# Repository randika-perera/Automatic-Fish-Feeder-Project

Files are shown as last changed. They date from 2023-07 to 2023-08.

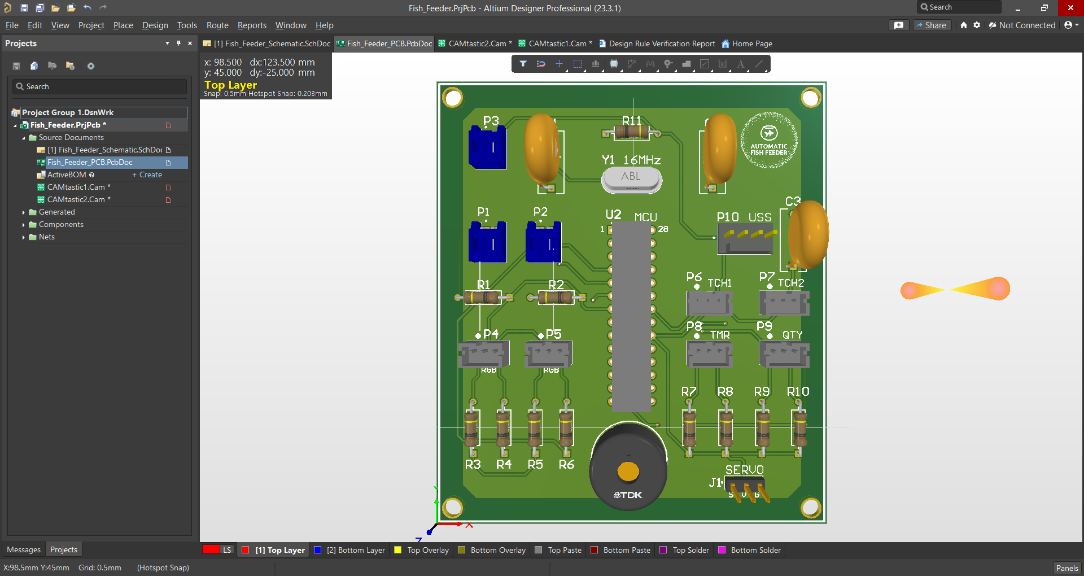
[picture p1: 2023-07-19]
PCB Design/Fish_Feeder/Images/3D View Top.png

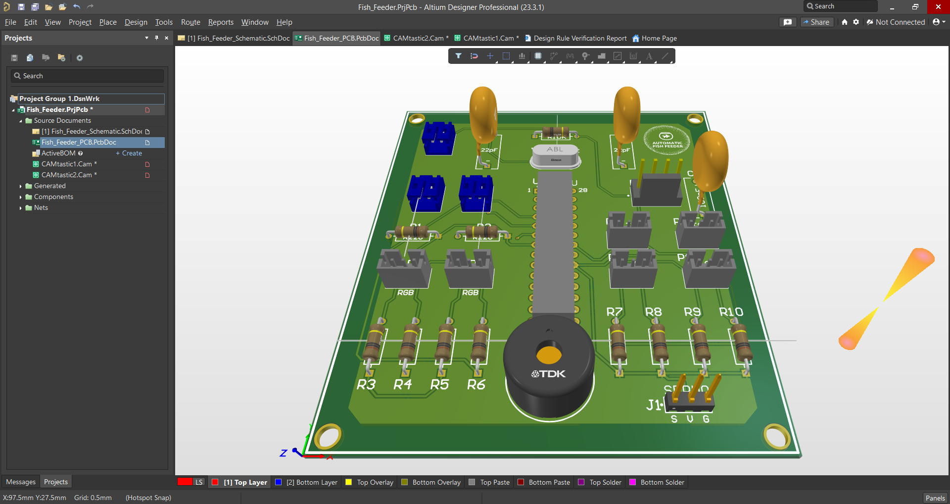
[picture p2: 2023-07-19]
PCB Design/Fish_Feeder/Images/3D View Side.png

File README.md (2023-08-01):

## Automatic Fish Feeder

The goal of this project was to make improvements to an existing market product and make it more marketable. </br>
This was an *individual project* carried out for the *Semester 4 Module EN2160 - Electronic Design Realization.*

The product that was implemented was an automatic fish feeder. </br>
The **improvements** and **extra features** that were incorporated to set it apart from existing products are as follows,
- ***Simple User Interface and Controls*** – Upon market research it was apparent that most of the existing products had heavily cluttered interfaces and control panels. Simplification of the user interface and hence improving the user experience was the biggest focus of this product.
- ***Mountable on both sides*** – This was designed to be mounted on either sides of a fish tank by incorporating replicated indicators and controls on 2 sides.
- ***Level Detection*** – Capable of indicating to the user when the fish food in the storage compartment has gone below a certain level. Indications were done redundantly using both sound and light indications for better notifying the user.
- ***Touch Sensor*** – Instead of using push buttons like existing market products, touch sensors were utilized.

The project involved designing the circuit from scratch according to the set requirements, fabrication of a printed circuit board, hand soldering components, circuit testing and design of a 3D printed enclosure to encase everything in a suitable form factor.

Software tools including *VSCode*, *Arduino IDE*, *Proteus Design Suite*, *Altium Designer* and *SolidWorks* were utilized.

The functional block diagram of the product is given below,

block_diagram

A photo of the final product is given below,



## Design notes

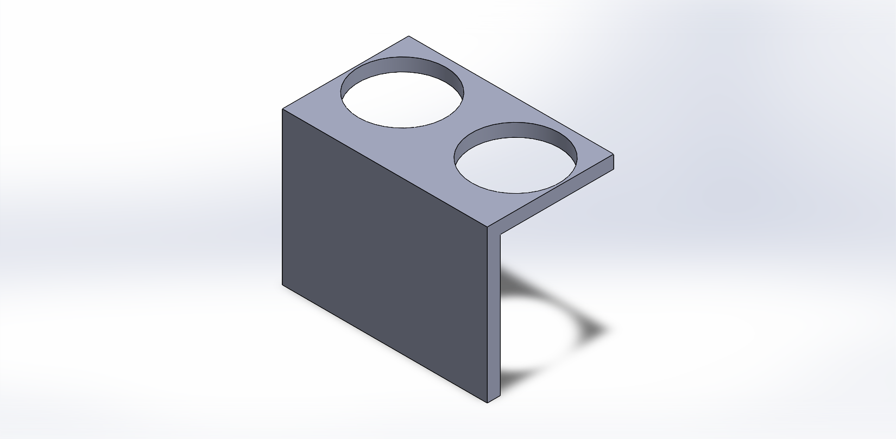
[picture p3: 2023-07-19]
Enclosure Design/Images/Ultrasonic Bracket.PNG

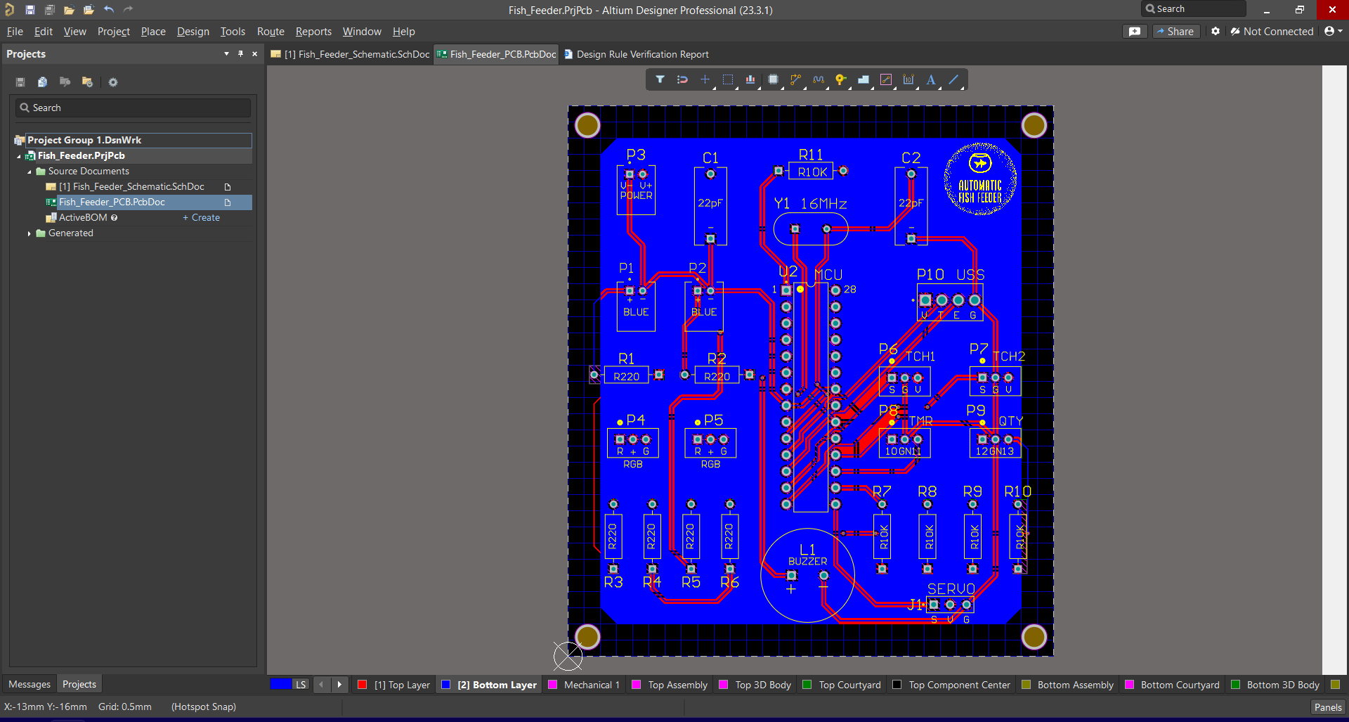
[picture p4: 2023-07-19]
PCB Design/Fish_Feeder/Images/Bottom Layer.png

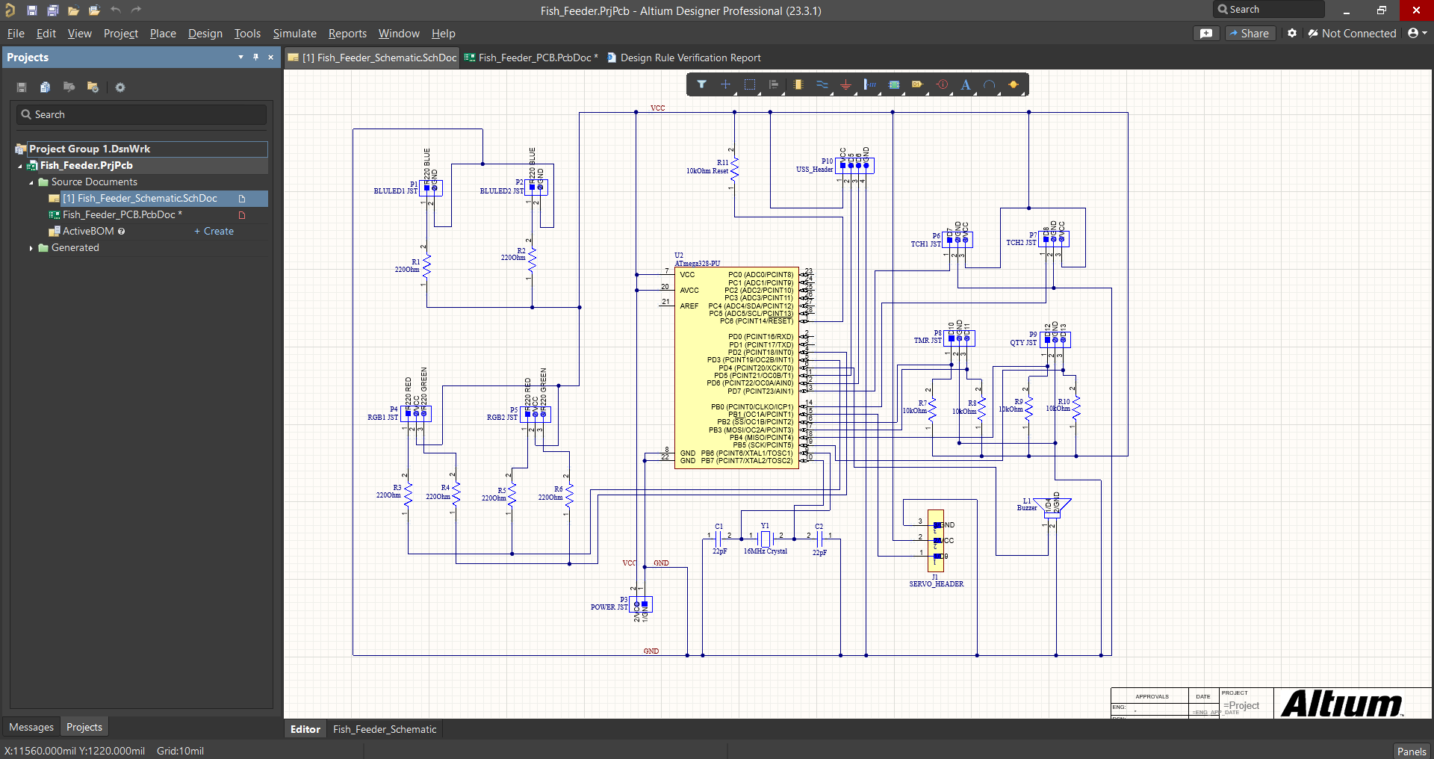
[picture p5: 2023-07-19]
PCB Design/Fish_Feeder/Images/Schematic.png

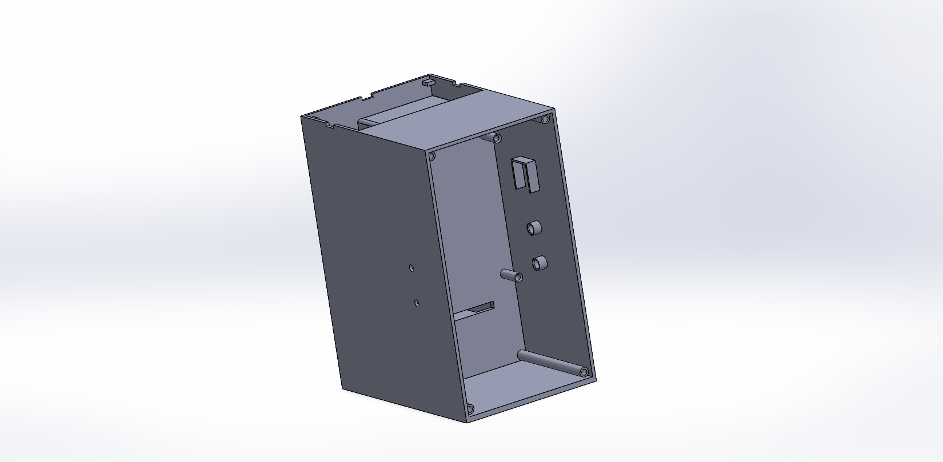
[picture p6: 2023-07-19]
Enclosure Design/Images/Main Body.PNG

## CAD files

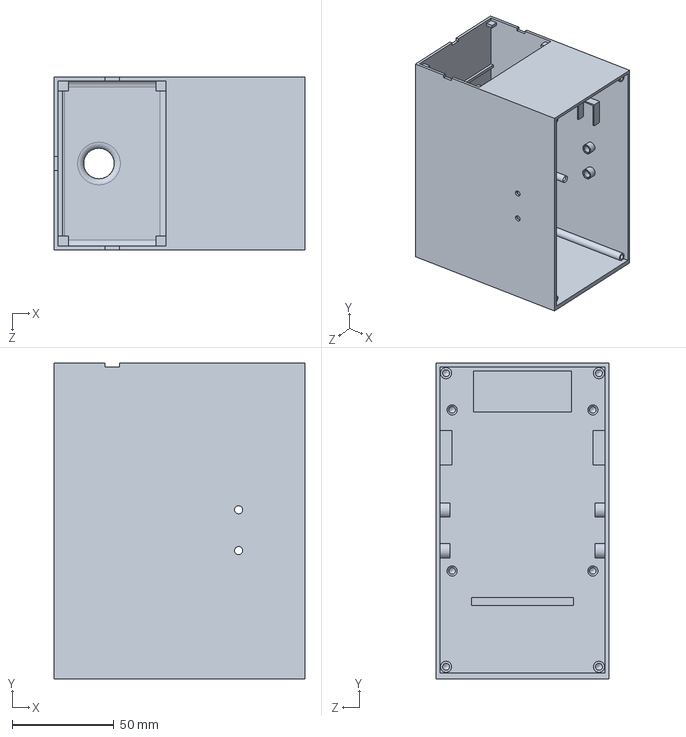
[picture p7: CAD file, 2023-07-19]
Enclosure Design/Main Body.SLDPRT
123.0 x 155.0 x 85.0 mm

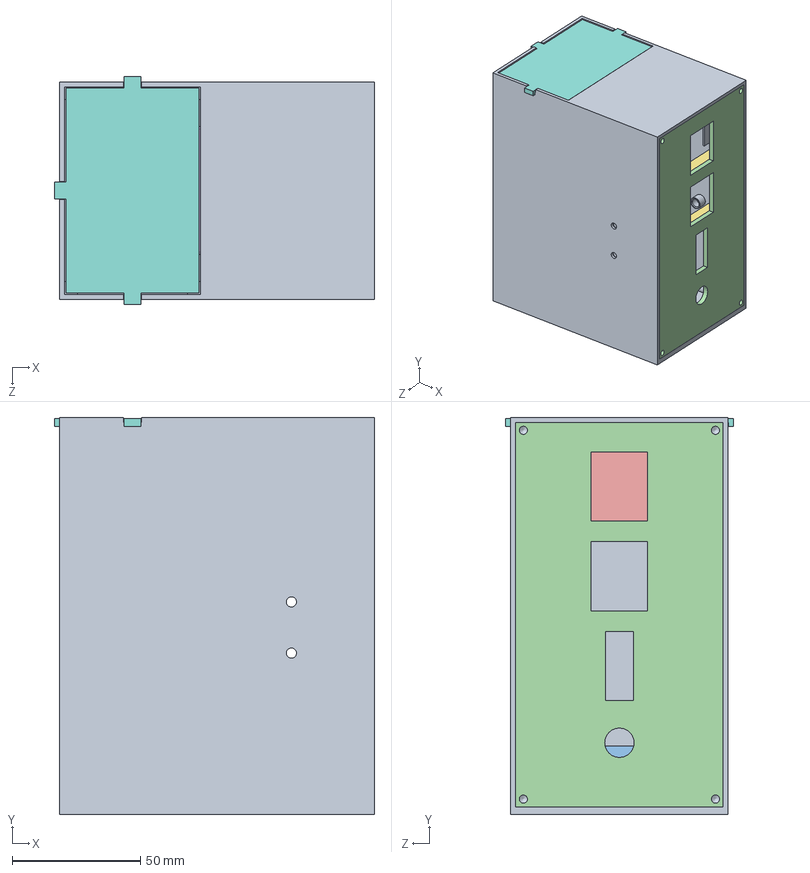
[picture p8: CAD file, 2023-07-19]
Enclosure Design/Assembly/Assembly of Full Enclosure.SLDASM
125.0 x 155.0 x 89.0 mm
Main Body
Servo Arm
Servo Bracket
Side Panel
Ultrasonic Bracket
Ultrasonic Hood
L Beam x 2
Top Lid Modified

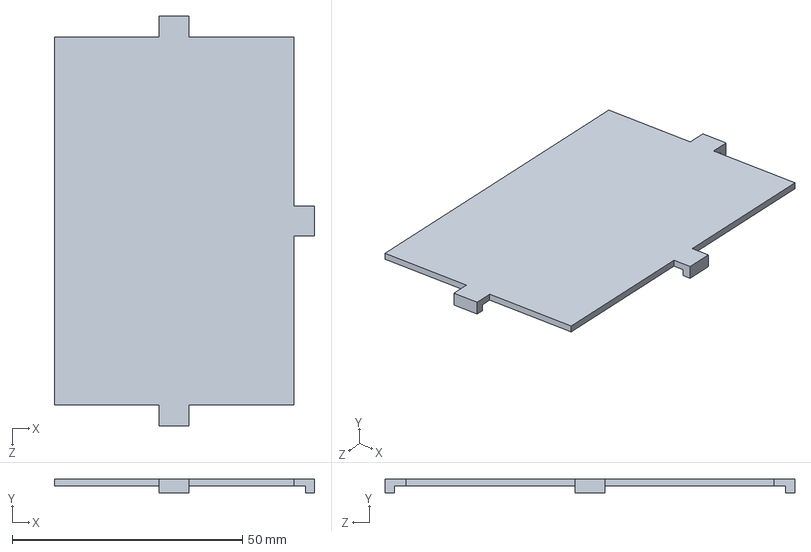
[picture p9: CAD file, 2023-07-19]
Enclosure Design/Assembly/Top Lid Modified.SLDPRT
56.5 x 3.00 x 89.0 mm

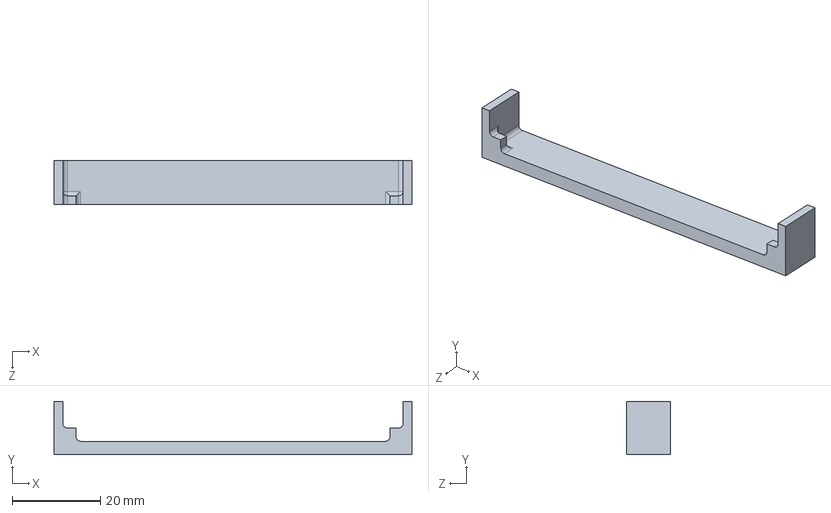
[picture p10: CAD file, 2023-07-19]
Enclosure Design/C Beam.SLDPRT
81.0 x 12.0 x 10.0 mm

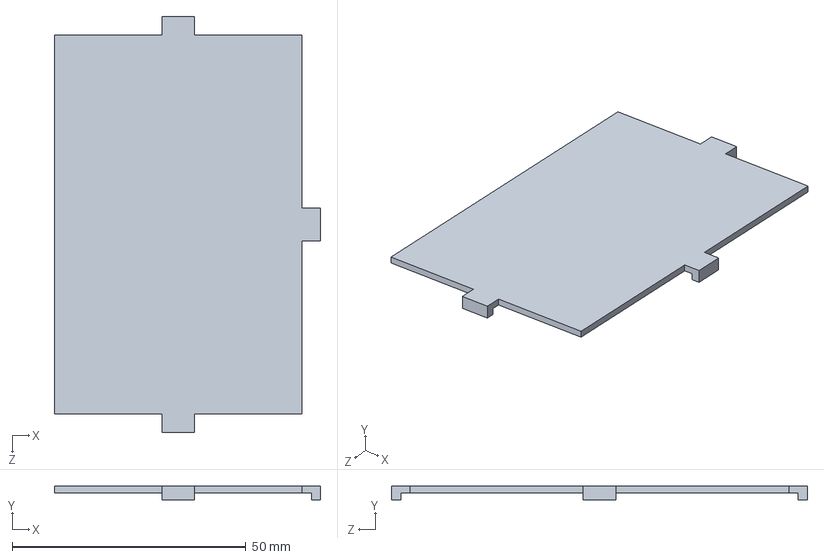
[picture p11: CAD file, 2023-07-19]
Enclosure Design/Assembly/Top Lid.SLDPRT
57.0 x 3.00 x 89.0 mm

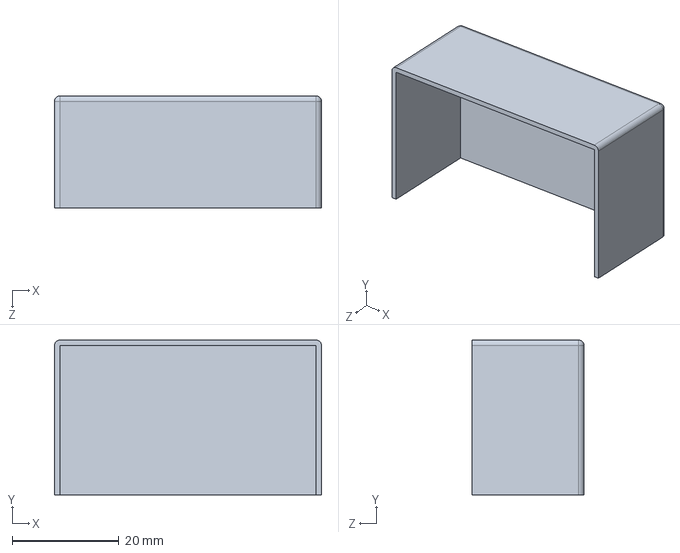
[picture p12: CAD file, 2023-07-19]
Enclosure Design/Ultrasonic Hood.SLDPRT
50.0 x 29.0 x 21.0 mm

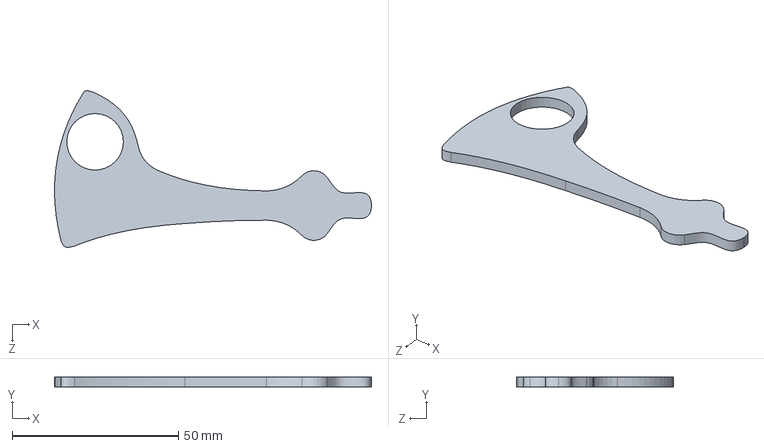
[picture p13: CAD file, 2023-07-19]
Enclosure Design/Assembly/Servo Arm.SLDPRT
95.4 x 3.00 x 47.1 mm

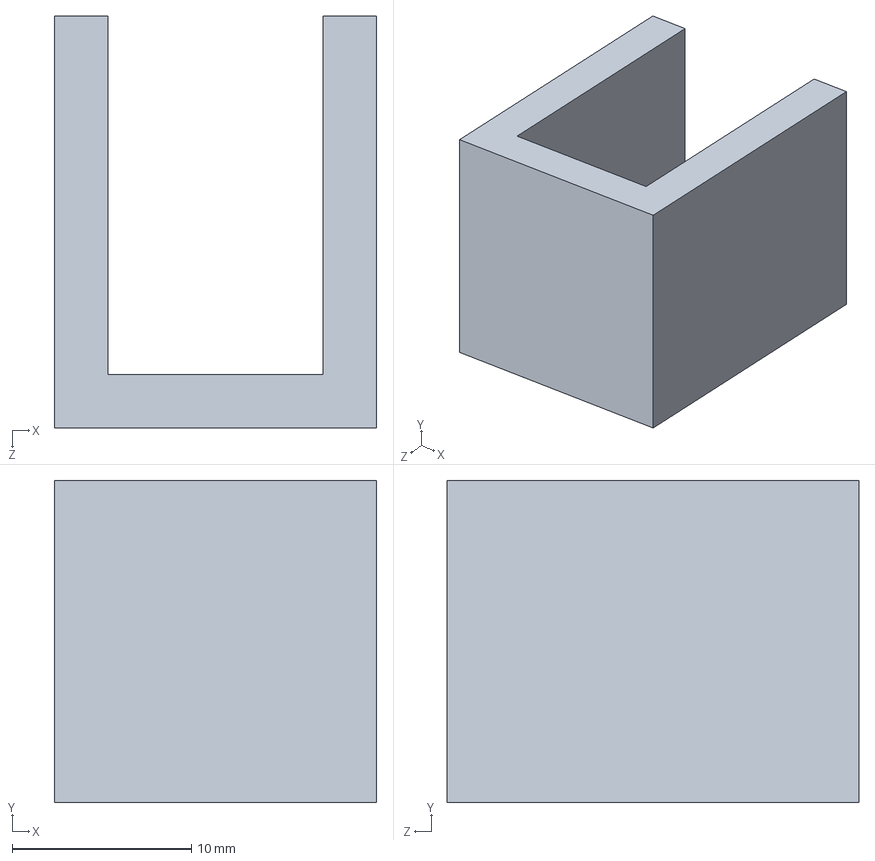
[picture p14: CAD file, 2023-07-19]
Enclosure Design/Servo Bracket.SLDPRT
18.0 x 18.0 x 23.0 mm

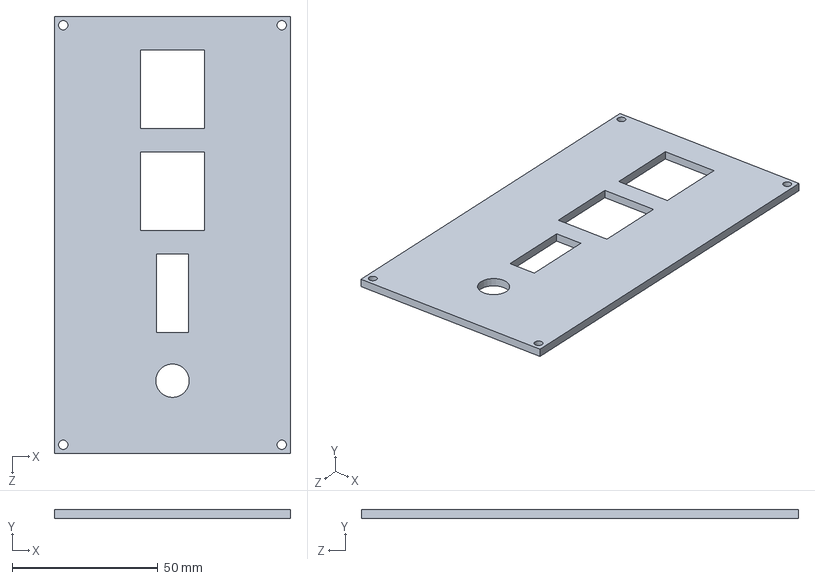
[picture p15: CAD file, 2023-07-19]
Enclosure Design/Assembly/Side Panel.SLDPRT
81.0 x 3.00 x 150.0 mm

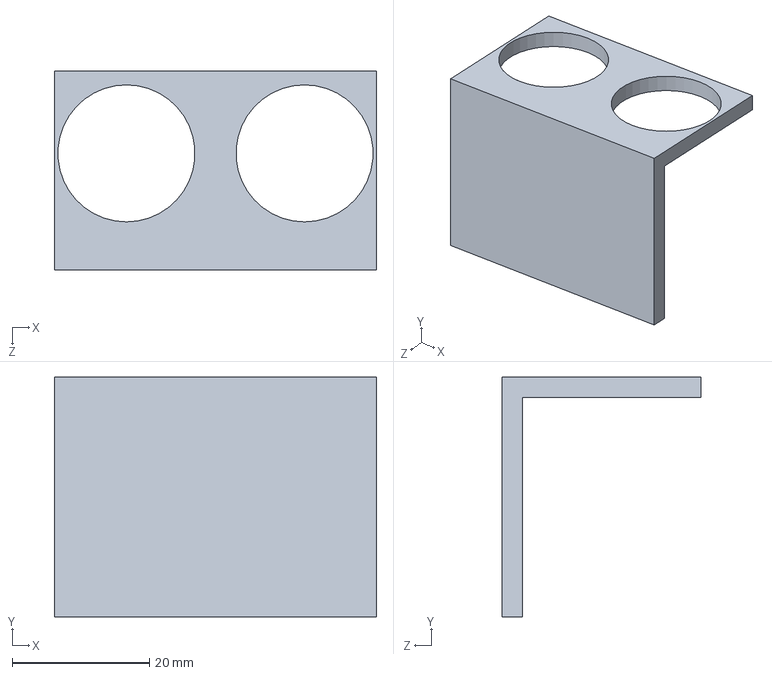
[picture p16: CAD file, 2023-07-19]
Enclosure Design/Assembly/Ultrasonic Bracket.SLDPRT
47.0 x 35.0 x 29.0 mm

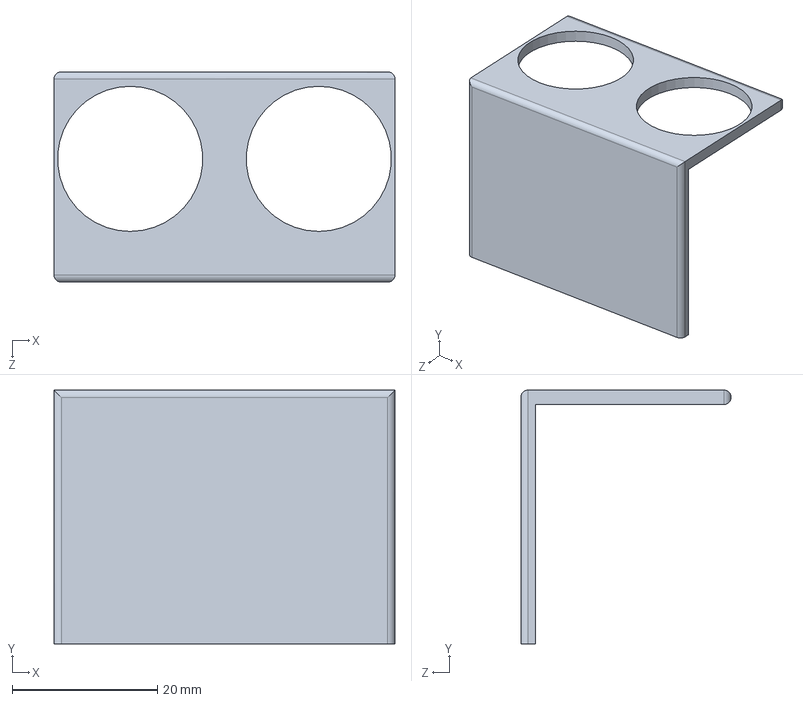
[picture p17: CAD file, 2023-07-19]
Enclosure Design/Ultrasonic Bracket.SLDPRT
47.0 x 35.0 x 29.0 mm

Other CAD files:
Enclosure Design/Assembly/Ultrasonic Hood.SLDPRT
Enclosure Design/C Beam.STL
Enclosure Design/Main Body.STL
Enclosure Design/Servo Arm.STL
Enclosure Design/Servo Bracket.STL
Enclosure Design/Side Panel.STL
Enclosure Design/Top Lid Modified.STL
Enclosure Design/Top Lid.STL
Enclosure Design/Ultrasonic Bracket.STL
Enclosure Design/Ultrasonic Hood.STL

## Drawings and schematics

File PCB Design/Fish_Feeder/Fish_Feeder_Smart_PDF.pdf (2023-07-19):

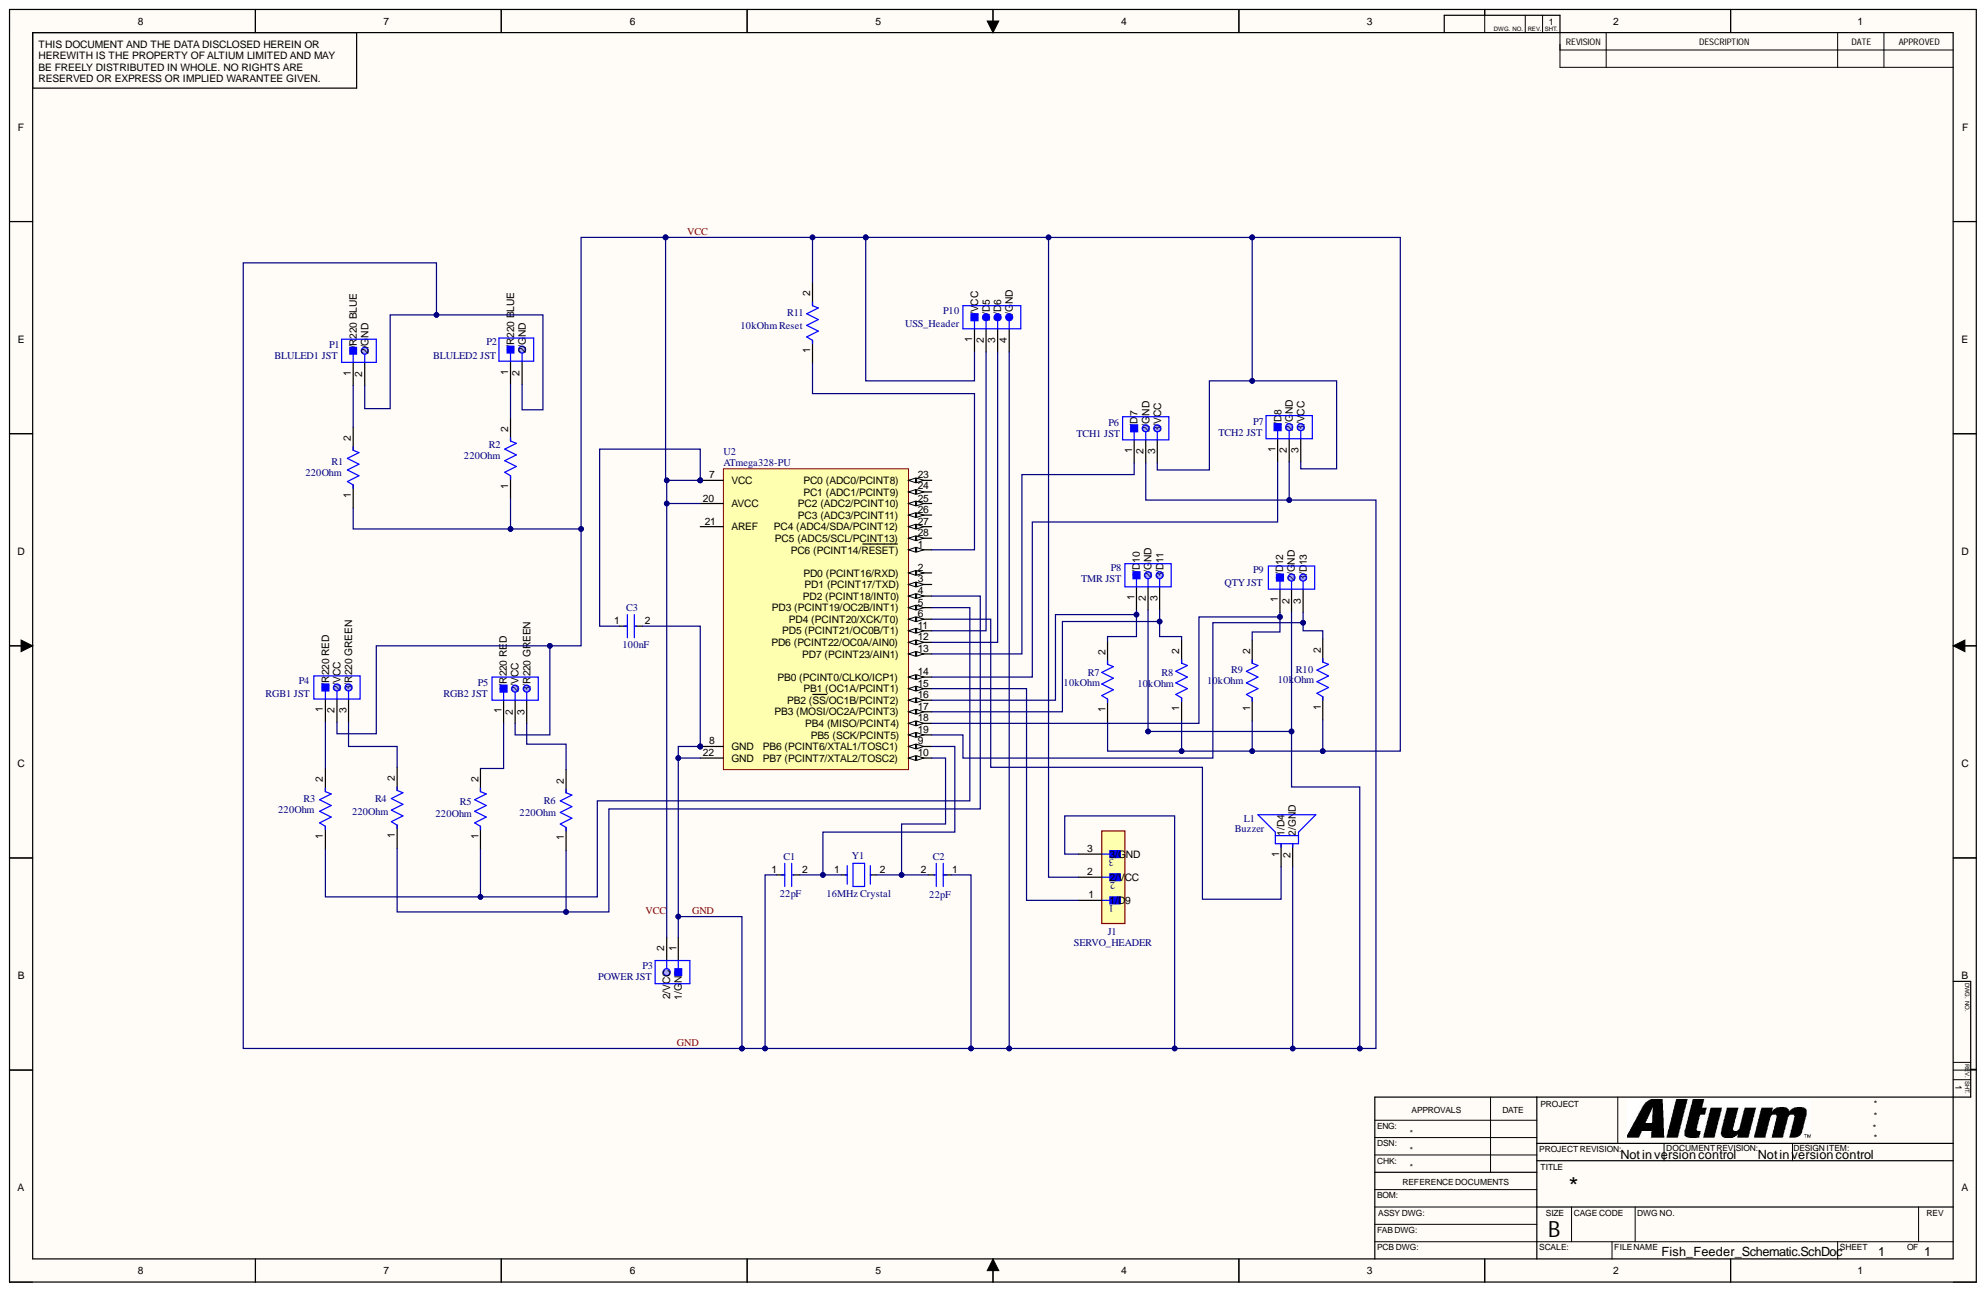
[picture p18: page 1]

T H I S D O C UME N T A N D T H E D AT A D I S C L O S E D H E R E I N O R H E R EWI T H I S T H E P R O P E R T Y O F A LT I UM L IMI T E D A N D MAY B E F R E E LY D I S T R I B U T E D I N WH O L E . N O R I G H T S A R E R E S E R V E D O R E X P R E S S O R IMP L I E D WA R A N T E E G I V E N . | C | REVI S I ON | DE SCRI PT I ON | DAT E | APPROVE D

1 4 | | R 7
1 5 | 1 0 | k O hm | 0 k O | 0 k O hm
1 6
1 7
1 8
1 9

REV. SHT. DWG. NO.

A P PROV A L S | DAT E | PROJE CT | ****

ENG :
** DSN:
CHK : | | TIT L E *

PROJECT RE VISION : Not i n v | ers DOCUM i o n c ENT RE o ntr o VISION l : Not i n | v DE ers SIGN IT i o n E c M o : ntr o l

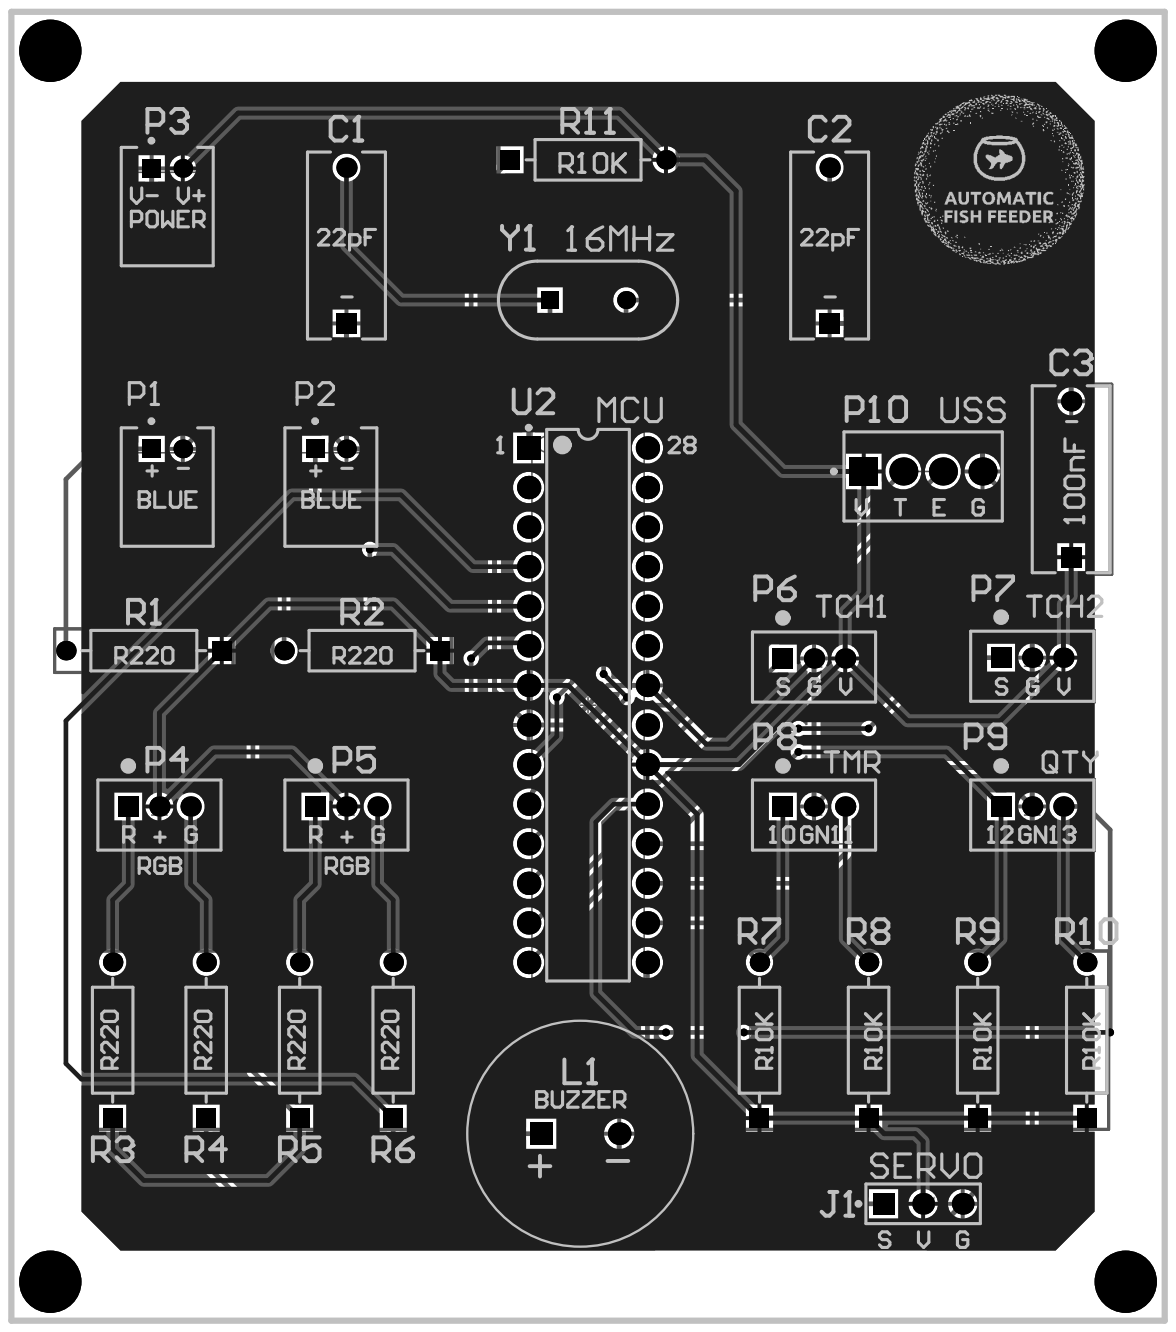
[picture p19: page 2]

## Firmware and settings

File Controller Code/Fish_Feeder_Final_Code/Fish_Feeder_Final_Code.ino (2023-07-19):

/*                                                      Automatic fish food dispenser                                                       */
/*                                        Copyright (C) 2023 Randika Perera.  All rights reserved.                                          */




/*-------------------------------------------  Importing Libraries and Declaration of I/O Pins  --------------------------------------------*/

#include <Servo.h>
Servo myservo;

const int RGB_green_pin=2;
const int RGB_red_pin=3;
const int buzzer_pin=4;
const int uss_trig_pin=5;
const int uss_echo_pin=6;
const int touch_sensor1_pin=7;
const int touch_sensor2_pin=8; 
const int servo_pin=9;
const int tmr_switch_INA_pin=10;
const int tmr_switch_INC_pin=11;
const int qty_switch_INA_pin=12;
const int qty_switch_INC_pin=13;


/*-----------------------------------------------  Declaration of variables and constants  -------------------------------------------------*/

const int fish_food_threshold_level=7;  //If distance between the sensor and surface of fish food is more than 7cm, fish food level is LOW. Else, HIGH.
int current_fish_food_level;

int distance;
int roundeddistance;
long t;

int tmr_switch_INA=1; //  1 or 0
int tmr_switch_INC=1; //  1 or 0
int qty_switch_INA=1; //  1 or 0
int qty_switch_INC=1; //  1 or 0

int tmr_state=1;  //  1:24hour, 2:12hour,   3:8hour
int qty_state=1;  //  1:Low,    2:Medium,   3:High

bool FF_level_state=HIGH; // LOW:Low fish food,  HIGH: Sufficient fish food
bool FF_alarm_state=LOW;  // Alarm can only ring in HIGH state.

const int servo_slot_closed_pos=87;   //Servo position for closed slot (default position).
const int servo_slot_open_pos=66;     //Servo position for opened slot.
int slot_open_delay;                  //Time for which slot remains opened. Depends on qty_state.

//CHANGE THESE DURATIONS AS REQUIRED FOR FINAL PRODUCT
const int low_duration=150;      //Duration to keep slot open for low quantity     : 0.15s  
const int medium_duration=350;   //Duration to keep slot open for medium quantity  : 0.35s  
const int high_duration=500;     //Duration to keep slot open for high quantity    : 0.50s  

unsigned long current_time=0;
unsigned long previous_fishfooddispense_time=0;
unsigned long previous_levelmeasurement_time=0;
unsigned long previous_fflalarm_time=0;

//CHANGE THESE INTERVALS AS REQUIRED FOR FINAL PRODUCT
unsigned long fishfooddispense_interval;                //Depends on tmr_state. If tmrstate=1:24hours, tmrstate=2:12hours, tmrstate=3:8hours.
const unsigned long hour_24_interval = 20000;           //In final product:24 hours. Here it is 20s.
const unsigned long hour_12_interval = 10000;           //In final product:12 hours. Here it is 10s.
const unsigned long hour_8_interval  =  5000;           //In final product: 8 hours. Here it is 5s.
const unsigned long levelmeasurement_interval=10000;    //In final product: 6 hours. Here it is 10s.
const unsigned long fflalarm_interval=10000;            //In final product: 6 hours. Here it is 10s.


/*------------------------------------------------------------  Setup & Loop  --------------------------------------------------------------*/

void setup() 
{

    /*
    Serial.begin(9600);
    */

    pinMode(RGB_green_pin,OUTPUT);
    pinMode(RGB_red_pin,OUTPUT);
    pinMode(buzzer_pin,OUTPUT);
    pinMode(uss_trig_pin,OUTPUT);
    pinMode(uss_echo_pin,INPUT);
    pinMode(touch_sensor1_pin,INPUT);
    pinMode(touch_sensor2_pin,INPUT);
    pinMode(tmr_switch_INA_pin,INPUT);
    pinMode(tmr_switch_INC_pin,INPUT);
    pinMode(qty_switch_INA_pin,INPUT);
    pinMode(qty_switch_INC_pin,INPUT);
    myservo.attach(servo_pin);
    myservo.write(servo_slot_closed_pos);
    digitalWrite(RGB_green_pin,HIGH);
    digitalWrite(RGB_red_pin,HIGH);
    
}


void loop() 
{

    /*
    Serial.print("Timer State =");
    Serial.println(tmr_state);
    Serial.print("Quantity State = ");
    Serial.println(qty_state);
    Serial.println("");
    */
    
    current_time=millis();

    read_switches_and_set_states();
    manual_key();
    release_fish_food_when_required();
    level_measurement();
    low_fish_food_alarm();

}


/*-------------------------------------------------------  User Defined Functions  ---------------------------------------------------------*/

void read_switches_and_set_states()     //Reads the rocker switches, determines the qty and tmr states, sets slot_open_delay and fishfooddispense_interval.
{
    tmr_switch_INA=digitalRead(tmr_switch_INA_pin);
    tmr_switch_INC=digitalRead(tmr_switch_INC_pin);
    qty_switch_INA=digitalRead(qty_switch_INA_pin);
    qty_switch_INC=digitalRead(qty_switch_INC_pin);

    if ((tmr_switch_INA==HIGH)&&(tmr_switch_INC==LOW))
    {
        tmr_state=1;    //Tmr 24hour
    }
    else if ((tmr_switch_INA==HIGH)&&(tmr_switch_INC==HIGH))
    {
        tmr_state=2;    //Tmr 12hour
    }
    else if ((tmr_switch_INA==LOW)&&(tmr_switch_INC==HIGH))
    {
        tmr_state=3;    //Tmr 8hour
    }

    if ((qty_switch_INA==HIGH)&&(qty_switch_INC==LOW))
    {
        qty_state=3;    //Qty Low
    }
    else if ((qty_switch_INA==HIGH)&&(qty_switch_INC==HIGH))
    {
        qty_state=2;    //Qty Medium
    }
    else if ((qty_switch_INA==LOW)&&(qty_switch_INC==HIGH))
    {
        qty_state=1;    //Qty High
    }
    
    if (qty_state==1)
    {
        slot_open_delay=low_duration;
    }
    else if (qty_state==2)
    {
        slot_open_delay=medium_duration;
    }
    else if (qty_state==3)
    {
        slot_open_delay=high_duration;
    }

    if (tmr_state==1)
    {
        fishfooddispense_interval=hour_24_interval;
    }
    else if (tmr_state==2)
    {
        fishfooddispense_interval=hour_12_interval;    
    }
    else if (tmr_state==3)
    {
        fishfooddispense_interval=hour_8_interval;
    }
}


void release_fish_food()        //Instantaneously releases fish food through the slot.    
{
    myservo.write(servo_slot_open_pos);
    delay(slot_open_delay);
    myservo.write(servo_slot_closed_pos);
}


void release_fish_food_when_required()    //Releases fish food according to the fishfooddispense timer.
{
    if ((current_time-previous_fishfooddispense_time)>=fishfooddispense_interval)
    {
        release_fish_food();
        previous_fishfooddispense_time=previous_fishfooddispense_time+fishfooddispense_interval;
    }
}


void manual_key()       //Reads both touch sensors continuously. If either is pressed, instantaneously releases fish food according to the currently selected qty state. Also resets timers.
{

    int tsi_1=digitalRead(touch_sensor1_pin);
    int tsi_2=digitalRead(touch_sensor2_pin);

    if ((tsi_1==HIGH)||(tsi_2==HIGH))
    {

        release_fish_food();

        //All 3 timers will get reset when manual key is pressed.
        previous_fishfooddispense_time=current_time;
        previous_levelmeasurement_time=current_time;
        previous_fflalarm_time=current_time;

    }

}


void level_measurement()        //According to levelmeasurement timer, this measures fish food level, sets FF_level_state and sets colour of the RGB led.
{
    if ((current_time-previous_levelmeasurement_time)>=levelmeasurement_interval)
    {

        current_fish_food_level=measure_distance_using_uss();

        if (current_fish_food_level>=fish_food_threshold_level)
        {
            FF_level_state=LOW;
        }
        else 
        {
            FF_level_state=HIGH;
        }

        //RGB Leds are common anode type. Output HIGH:OFF, Ouput LOW:ON.
        if (FF_level_state==LOW)
        {
            digitalWrite(RGB_green_pin,HIGH);   //Off green led
            digitalWrite(RGB_red_pin,LOW);      //On red led
        }
        else
        {
            digitalWrite(RGB_red_pin,HIGH);     //Off red led
            digitalWrite(RGB_green_pin,LOW);    //On green led
        }

        previous_levelmeasurement_time=previous_levelmeasurement_time+levelmeasurement_interval;

    }
}


int measure_distance_using_uss()        //Measures and returns the distance from ultrasonic sensor to surface of fish food (in cm).
{
    digitalWrite(uss_trig_pin,HIGH);
    delayMicroseconds(10);
    digitalWrite(uss_trig_pin,LOW);
    t=pulseIn(uss_echo_pin,HIGH);
    distance=t*330/2/10000;
    roundeddistance=round(distance);
    return roundeddistance; 
}


void low_fish_food_alarm()      //Rings the alarm according to fflalarm timer.
{

    if (FF_level_state==HIGH)
    {
        FF_alarm_state=LOW;
    }

    if ((FF_level_state==LOW)&&(FF_alarm_state==LOW))
    {
        FF_alarm_state=HIGH;
        previous_fflalarm_time=millis();
    }

    if ((FF_alarm_state==HIGH)&&((current_time-previous_fflalarm_time)>=fflalarm_interval))
    {
        alarm();
        FF_alarm_state=LOW;
        previous_fflalarm_time=previous_fflalarm_time+fflalarm_interval;
    }
}


void alarm()        //Simulates an alarm using an active buzzer.
{
    digitalWrite(buzzer_pin,HIGH);
    delay(200);
    digitalWrite(buzzer_pin,LOW);
}




/*-------------------------------------------------------------------------------------------------------------------------------*/
